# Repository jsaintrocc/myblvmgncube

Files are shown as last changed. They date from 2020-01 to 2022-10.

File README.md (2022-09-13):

# MY BLV MGN Cube

## Table of contents
  1. [Introduction](#introduction)
  2. [Bill of materials](manual/bom.md)
  3. [Printed parts](https://docs.google.com/spreadsheets/d/e/2PACX-1vTVx7BvB3V7CozF2l4eWkNntWrHSjOawmrsi_bRSVxQLIGVlfZTYEGp8a6fHpENV6hV2cn9PrDLHHl0/pubhtml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)
  4. [Print Settings](https://docs.google.com/spreadsheets/d/e/2PACX-1vTgPZb2P_rigplUG4TBjnBd7A5v86qJmxN26Bf9Z0P1HwILFovxDry4oiuArPlMLLYwE4DXcqXhaWn0/pubhtml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)
  5. [Assembly Guide](manual/guide/README.md)
  6. [License](#license)
  7. [Credits and inspiration](#credits-and-inspiration)

## Introduction
This documents my journey building the MGN BLV 3D Printer designed and graciously contributed to the world by [Ben Levi](parts/source/README.md). My goal is to provide a guide that others can follow to build their own cubes. This guide provides instructions for my specific build as detailed below. If your configuration is different keep that in mind when following the directions.

### Build Picture
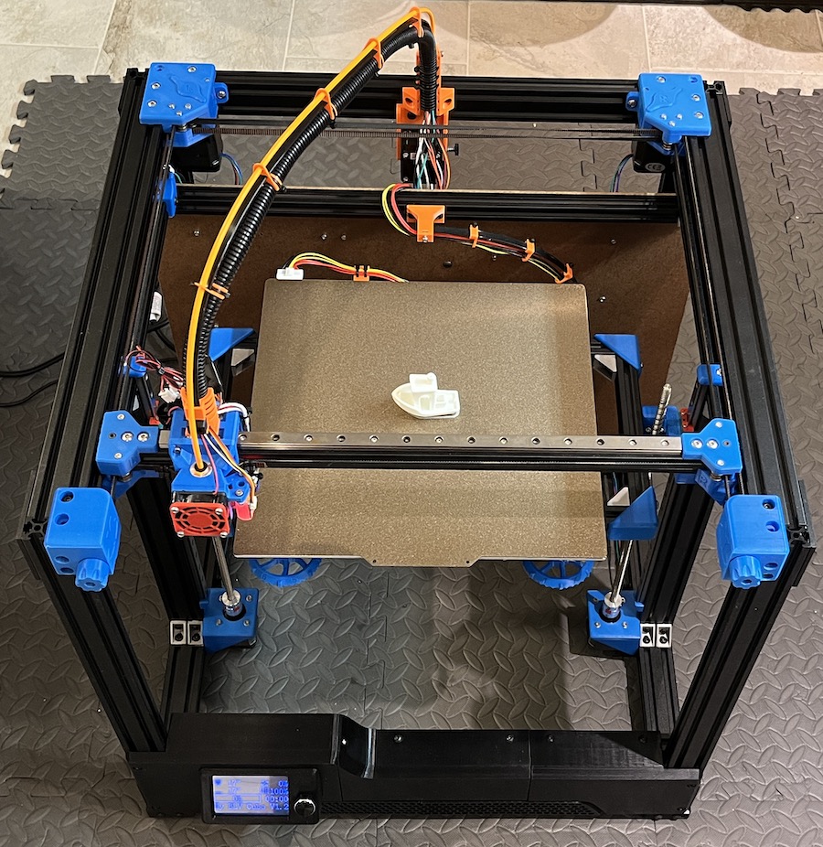
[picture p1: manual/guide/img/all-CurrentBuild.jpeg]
My Printer


### My Build Specifications
* Standard 365mm build height frame (The one listed on BLV's site)
* E3D V6 Cloned Hotend
* BLTouch ABL probe
* SKR v1.4 controller
* TMC2208 stepper drivers
* BIGTREETECH TFT35 <u>V3</u> LCD touch screen
* 3D printed parts

## License

Licensed under [CC BY-NC-SA 3.0](https://creativecommons.org/licenses/by-nc-sa/3.0/)

## Credits and inspiration
This work is based on the [BLV mgn Cube - 3d printer](https://www.blvprojects.com/blv-mgn-cube-3d-printer) graciously donated the the community by [Ben Levi](https://www.facebook.com/blevi?fref=gs&dti=371460246914851&hc_location=group_dialog) and is licensed under [CC BY-NC-SA 3.0](https://creativecommons.org/licenses/by-nc-sa/3.0/).  Any modified files will be clearly labelled.

Lots of tips and pointers from watching [Fugatech3D's live stream on his build](https://www.youtube.com/user/fuganater987)

Also the documentation and style modifications were greatly inspired by [Greg Saun's Work](https://github.com/gregsaun/bear_extruder_and_x_axis/blob/master/README.md)

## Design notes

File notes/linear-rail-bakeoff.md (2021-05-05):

# Liner Rail Bakeoff

## What's This Now?

I'm doing this to show some examples of the "economy" rails I've purchased and things to look out for. Linear rails for 3D printers are available at anywhere from $15/$200. Here's a detailed comparison of some of the lower end models I've purchased to hopefully provide some guidance and save you major headaches later on.

## TLDR

LDO would be my 1st pick followed by Robodigg and last would be CNA. For CNA I'd expect 2 out of 5 rails to be unusable and from the poor machining you'd probably introduce artifacts that would be very hard to fix. While Robotdigg is somewhat comparable keep in mind that coming from Aliexpress means to take a definite risk trying to return items and shipping times will be in weeks if not months.

### The Rails

| Part Number | Manufacturer | Cost + Shipping | Example Links |
|---|---|---|---|
| MGN12H 400mm Linear Rail | [CNA/RDBB](img/CNAManufacturer.JPG) (Cheap Cheap Cheap) | $20.92 | [Aliexpress](https://www.aliexpress.com/item/32829826159.html?spm=a2g0s.9042311.0.0.27424c4dwPelhS) |
| SS-MGN12-1H-400mm | RobotDigg (Middle Quality) | $34.20 | [Aliexpress](https://s.click.aliexpress.com/e/_AA8VKF) |
| LDO-MGN12H | LDO (Best Quality) | $34.80 (Free ship over $60) | [PrintedSolid](https://www.printedsolid.com/products/ldo-linear-rail-mgn12h-with-one-carriage-in-300-400-500-700mm-lengths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) [Filastruder](https://www.filastruder.com/products/ldo-linear-rails) [VRParts](https://vrparts.de/.../ldo-linearschienen-mgn12h-1r-l-400mm) |

### Tools I used

| Description | Details | Example Links |
|---|---|---|
| iPhone | What I took the pictures with | [Apple](https://www.apple.com/iphone/) |
| Clip-On Macro Lens | 20x Macro is what I used in this kit | [Amazon](https://amzn.to/3eeCqLU) |
| Smart Phone Tripod | To keep it steady | [Amazon](https://amzn.to/3dtMaTI) |

## Surface Finish Comparison On the Carriage

### End Finish

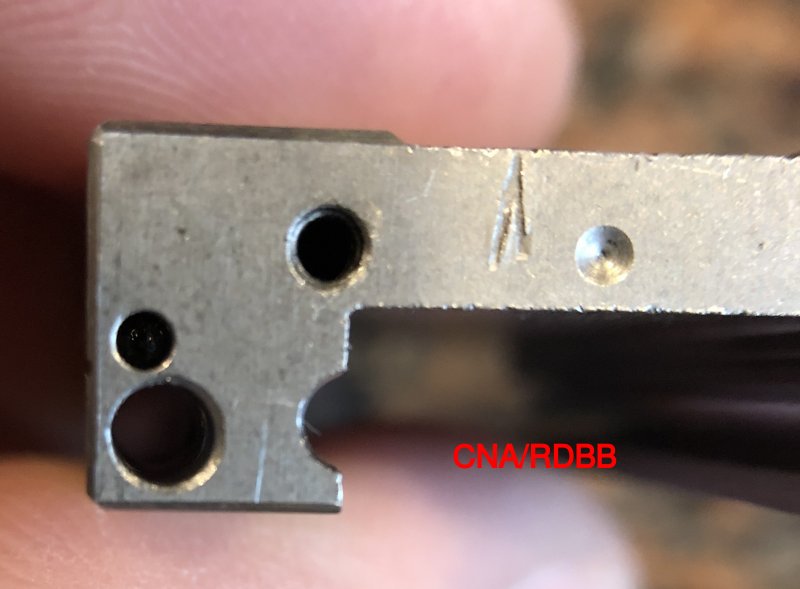
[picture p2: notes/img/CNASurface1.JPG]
CNARDBB Surface 1
 
**Surface is covered in marks. Even though it's cosmetic this one is particularly deep**

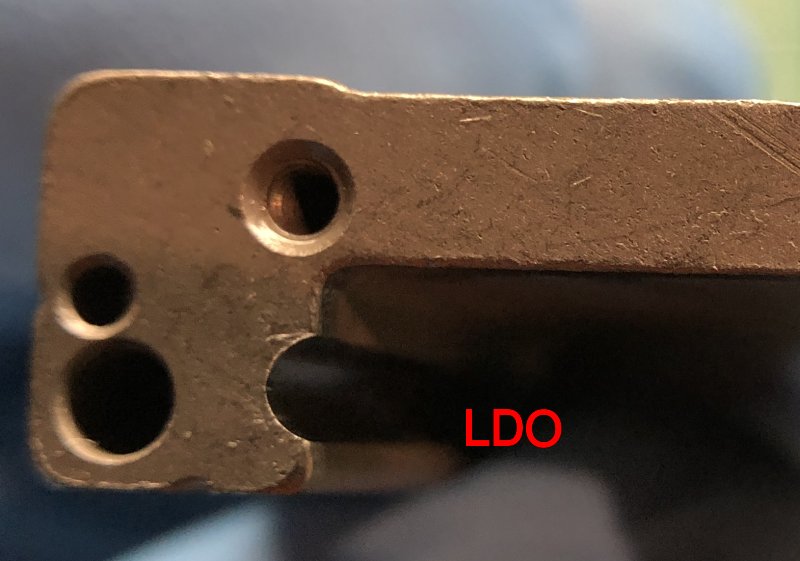
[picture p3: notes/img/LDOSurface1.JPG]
LDO Surface 1
 
**Similar tooling marks but nothing too deep**

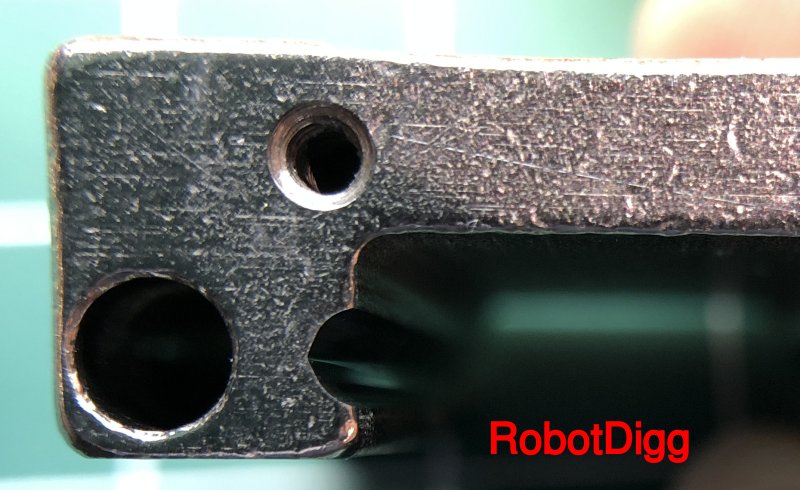
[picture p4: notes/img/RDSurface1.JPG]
RoboDigg Surface 1
 
**Many superficial scratches. There's a thick Chrome/Electroplated surface treatment here**

### Underside Finish

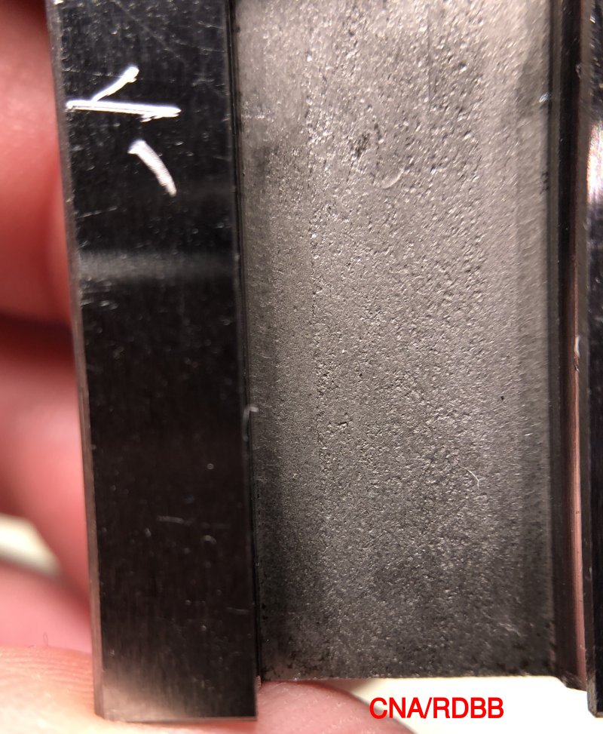
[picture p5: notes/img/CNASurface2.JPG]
CNARDBB Surface 2

**The grain in this picture really shows the poor quality of the alloy they're using. The mark in the upper left is actually engraved**

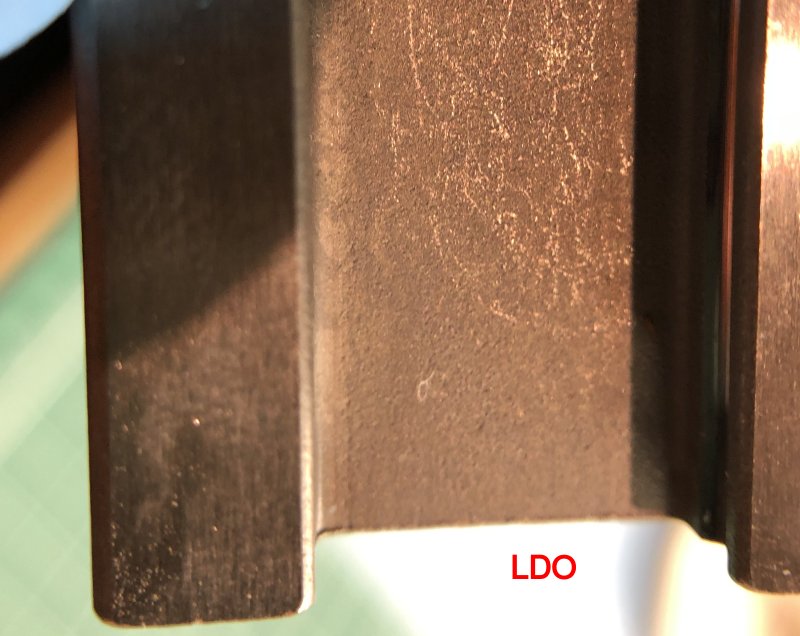
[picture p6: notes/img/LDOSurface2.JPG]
LDO Surface 2

**Little hard to see but the grain is much smaller and more consistent**

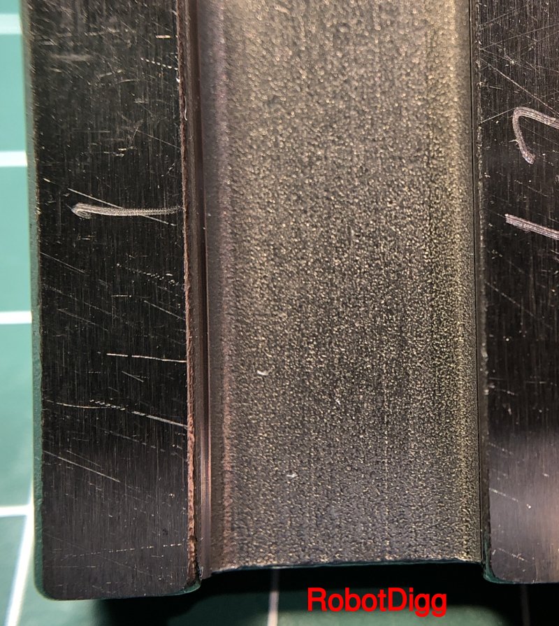
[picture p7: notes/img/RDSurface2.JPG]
RoboDigg Surface 2

**More of those etching marks but not too bad. However my 2nd carriage had some [missing Chrome on the underside](img/RDChromePlating.JPG)**

### Race/Return End Finish

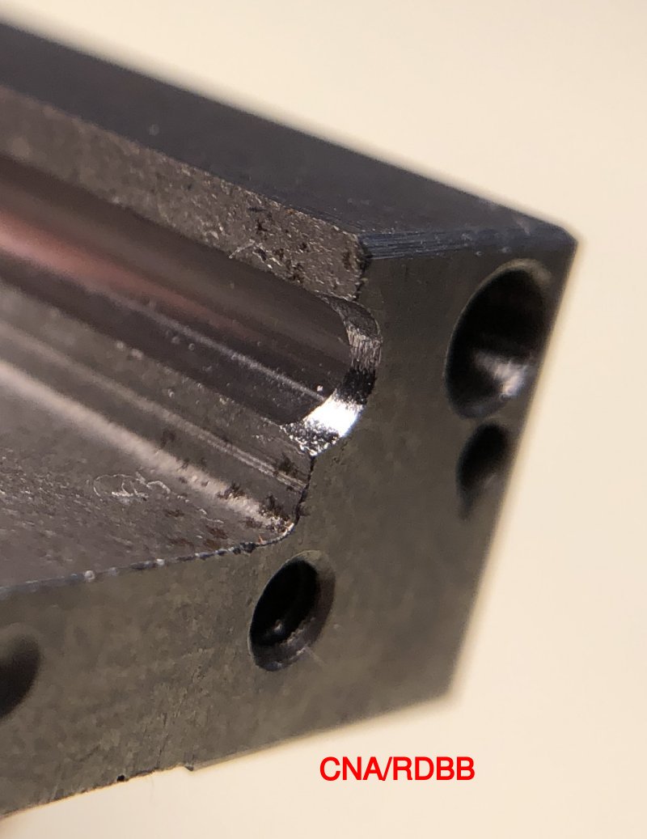
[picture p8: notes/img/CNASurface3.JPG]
CNARDBB Surface 3

**The alloy they're using is really terrible. Notice that the race has a hand filed bevel on it**

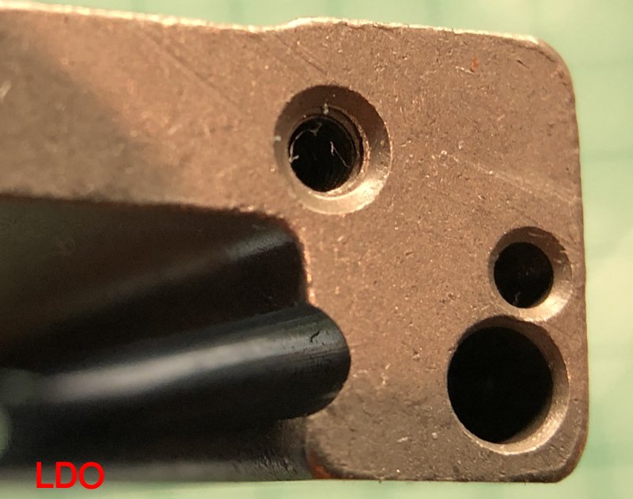
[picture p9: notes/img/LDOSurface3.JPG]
LDO Surface 3

**Here you can see that the machining is just better. The tolerances are much tighter**

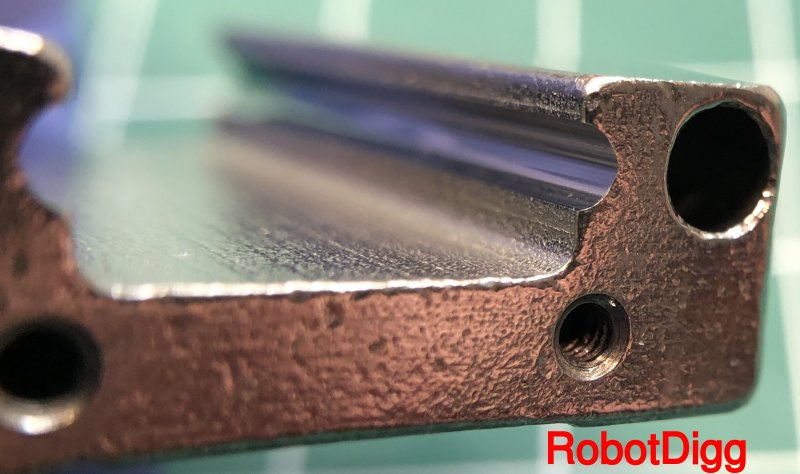
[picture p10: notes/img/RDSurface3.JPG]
LDO Surface 3

**Edges aren't very crisp. I'm guessing that's from the Chroming. This is less of an issue for RobotDigg because of something smart they did with PTFE liners. More on that later**

### Race Finish

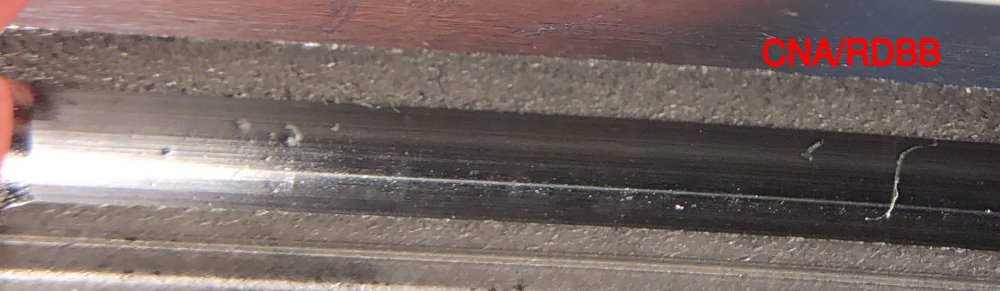
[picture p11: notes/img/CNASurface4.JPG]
CNARDBB Surface 4

**This is the important bit. Look at those pits and imperfections**

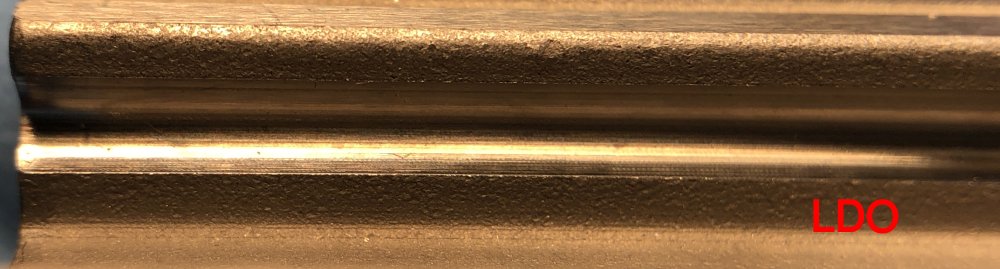
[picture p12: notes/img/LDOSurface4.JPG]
LDO Surface 4

**Machining on the race here is much better than CNA**

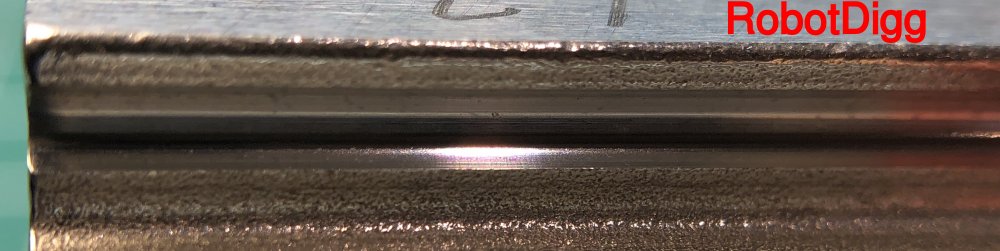
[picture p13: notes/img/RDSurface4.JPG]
RobotDigg Surface 4

**Machining on the race is comparable to LDO and much better than CNA. This is where the machining really counts!!**

### Ball Return Channels

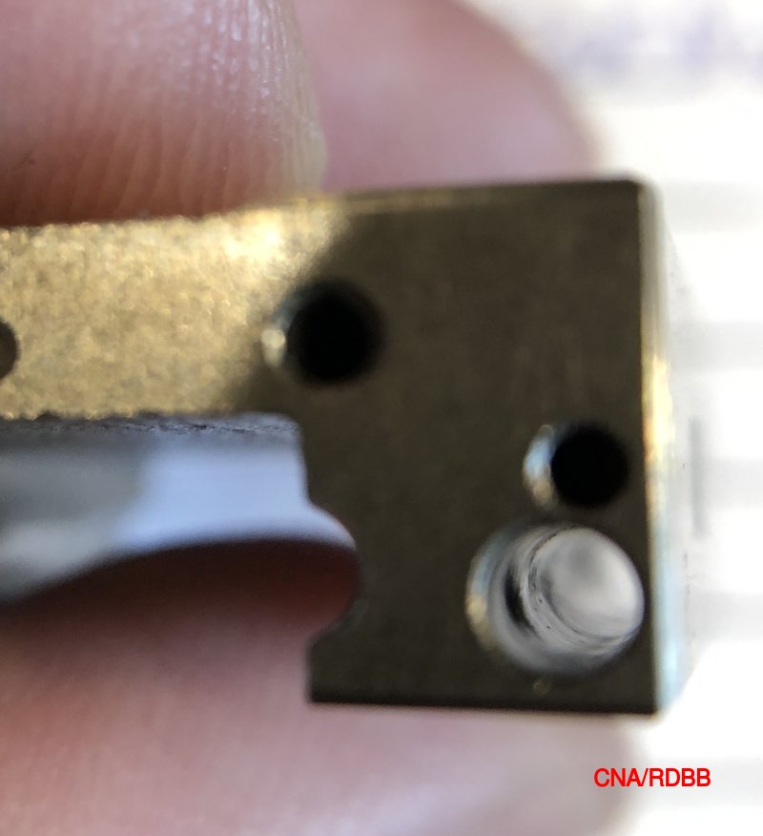
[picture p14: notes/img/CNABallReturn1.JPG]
CNARDBB Ball Return 1

**Look at those bumps. Bearings are not going to like that**

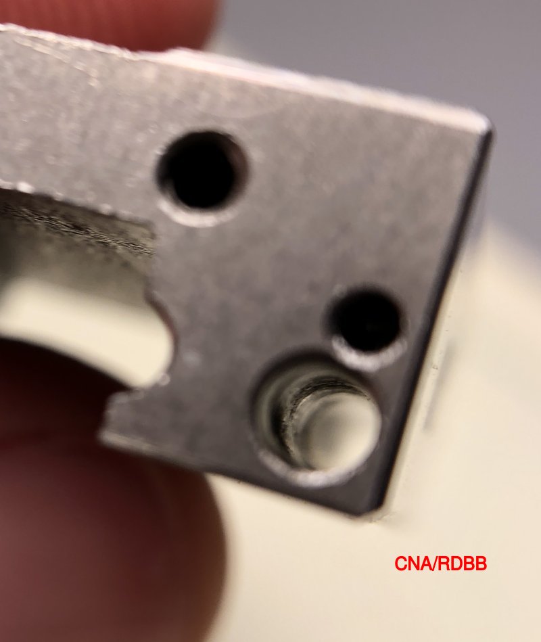
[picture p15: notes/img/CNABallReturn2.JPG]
CNARDBB Ball Return 2

**More bumps. Rough!!**

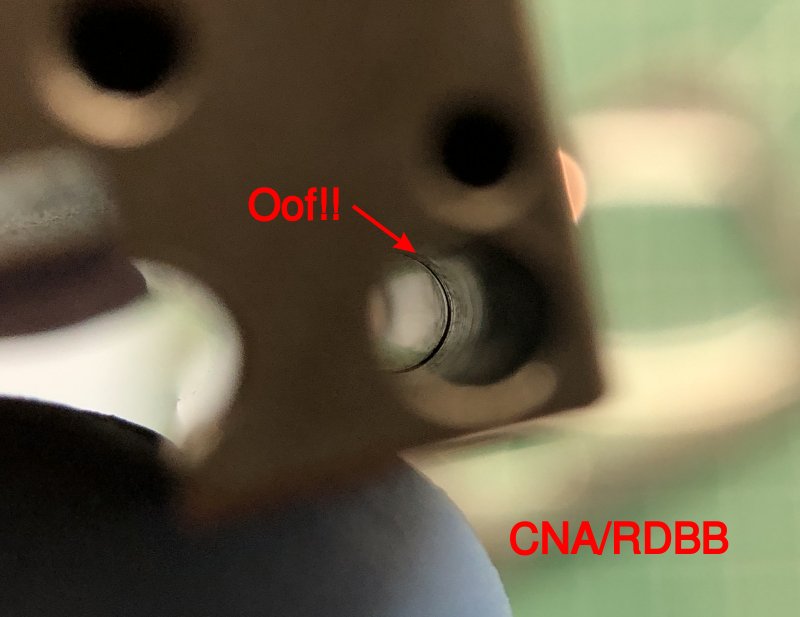
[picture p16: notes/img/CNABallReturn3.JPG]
CNARDBB Ball Return 3

**From a 2nd rail I got. That's a noticeable lip inside the ball return. This rail feels like gravel by the way**

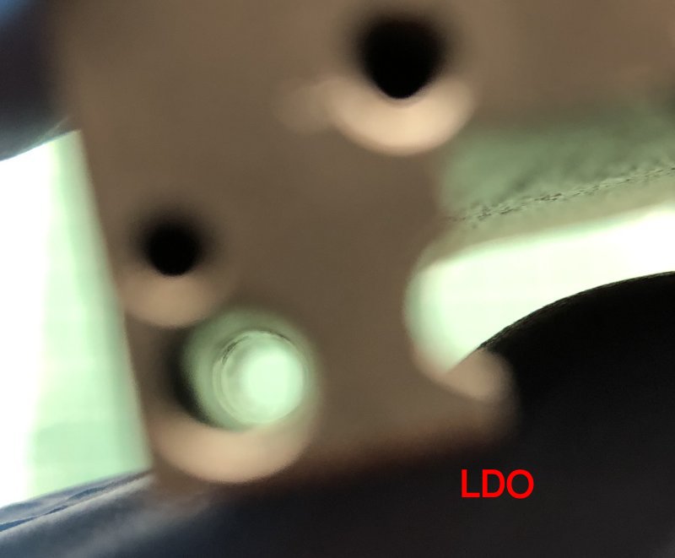
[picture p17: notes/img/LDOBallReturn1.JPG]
LDO Ball Return 1

**Not perfect but way better than CNA**

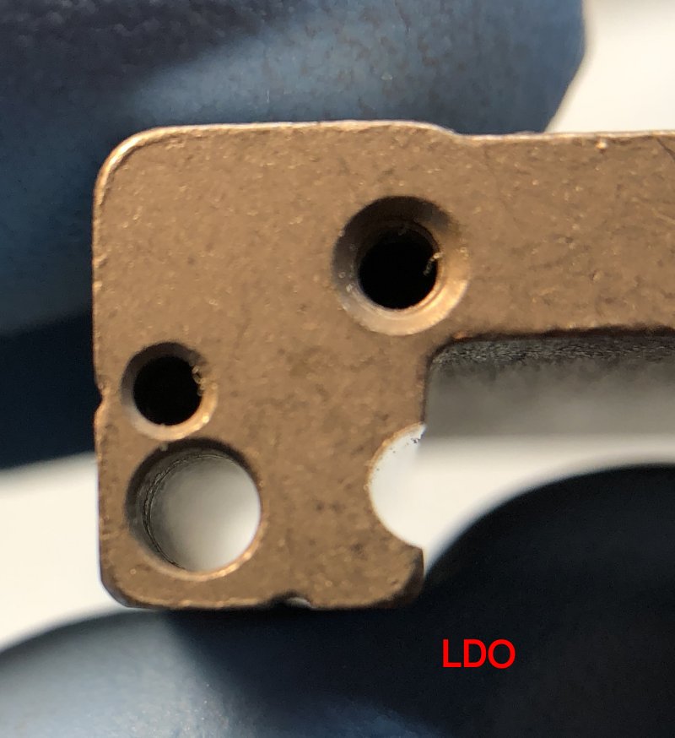
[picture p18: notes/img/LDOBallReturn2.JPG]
LDO Ball Return 2

**Not perfect but way better than CNA**

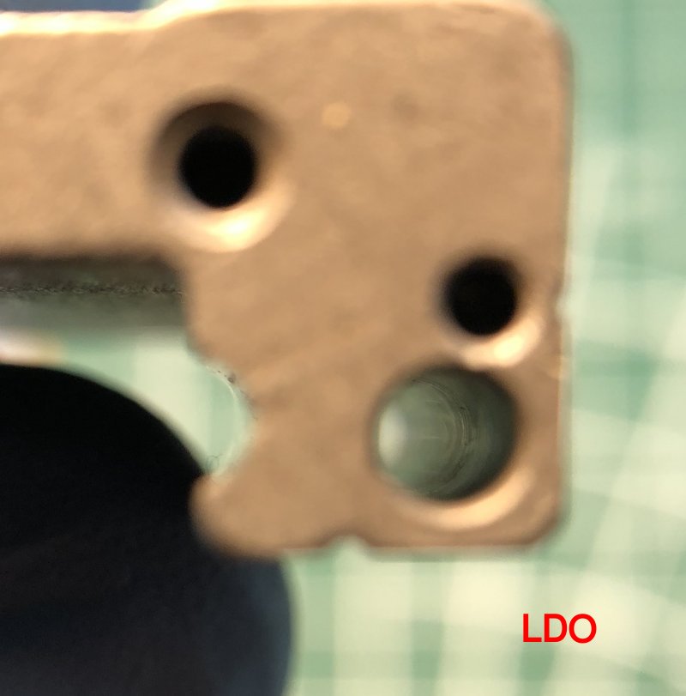
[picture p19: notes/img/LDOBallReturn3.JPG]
LDO Ball Return 3

**This one looks pretty good**

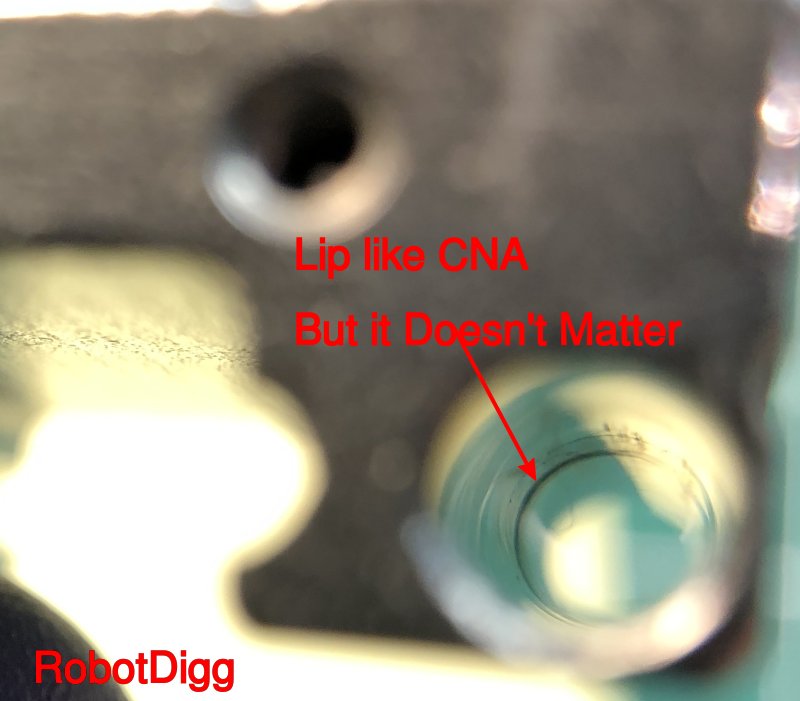
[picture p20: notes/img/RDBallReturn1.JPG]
RD Ball Return 1

**This shot doesn't really matter because of the smart engineering in the next step**

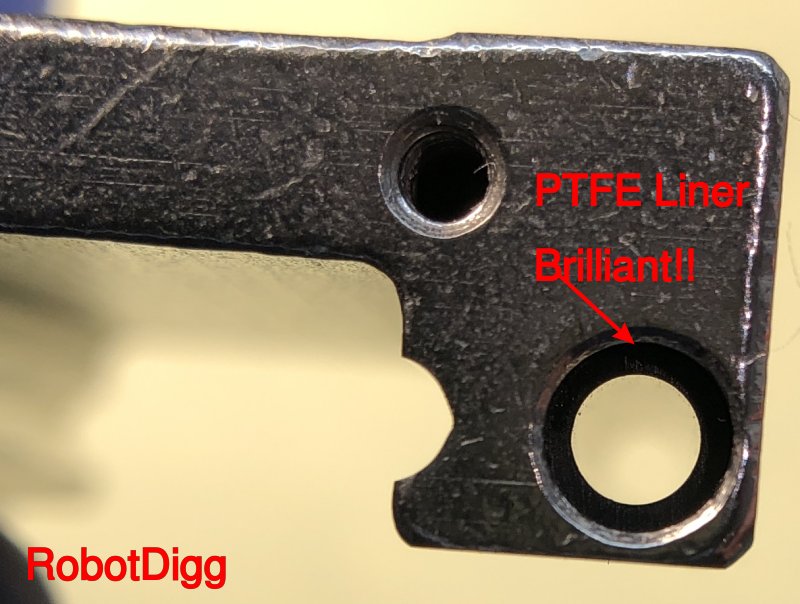
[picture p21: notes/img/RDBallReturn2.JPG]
RD Ball Return 2

**This liner means the machining isn't an issue and for our light application this will work great**

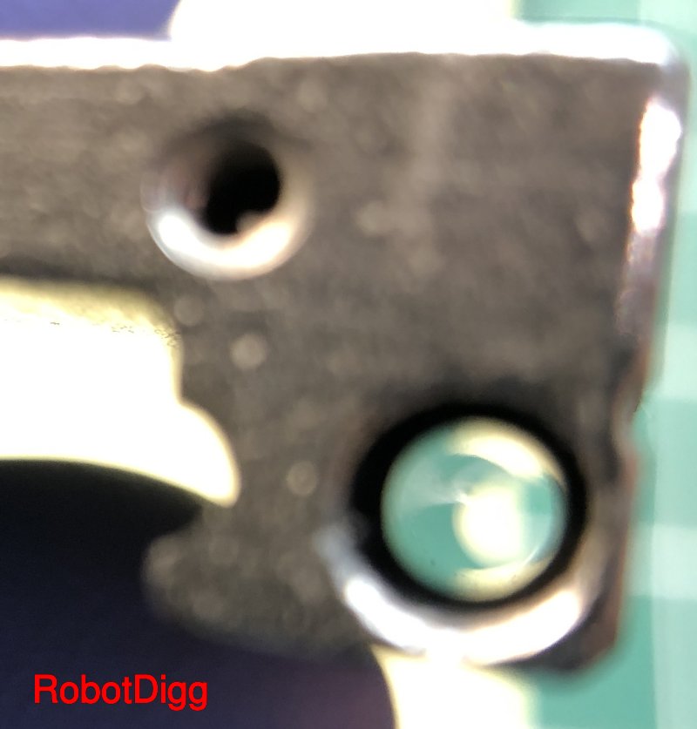
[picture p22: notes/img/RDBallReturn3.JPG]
RD Ball Return 3

**Hard to get a good shot as the liner is nearly mirror smooth**

### Ball Bearings

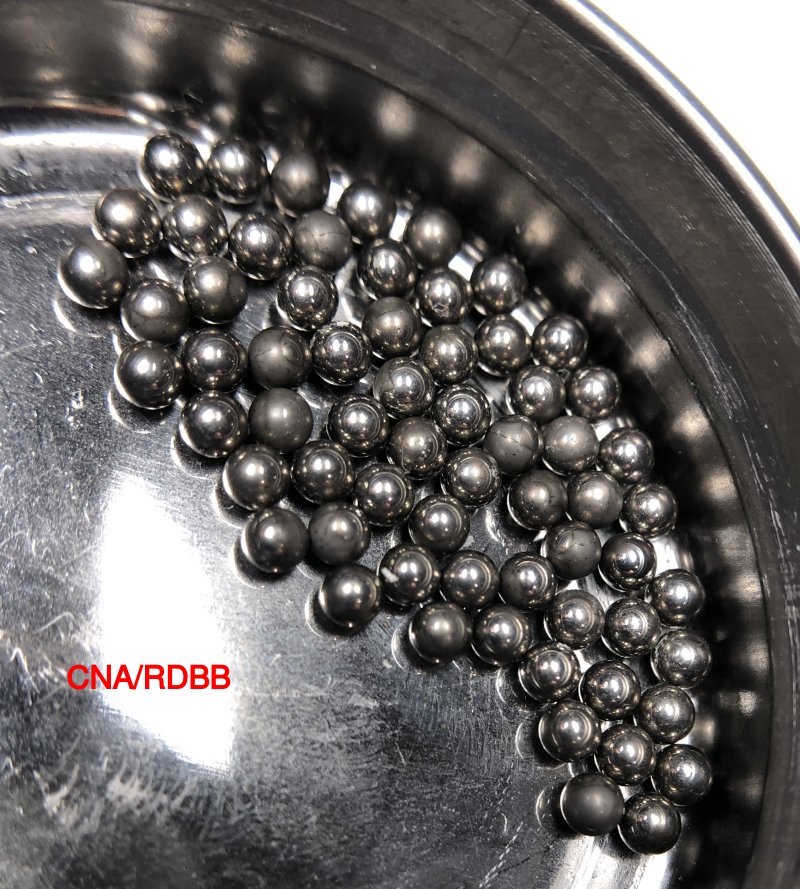
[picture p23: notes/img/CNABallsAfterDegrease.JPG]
CNARDBB Chrome Balls After Degrease

**Accidentally Left them in Simple Green overnight and this happened. Guessing this shows how thinly chromed they are**

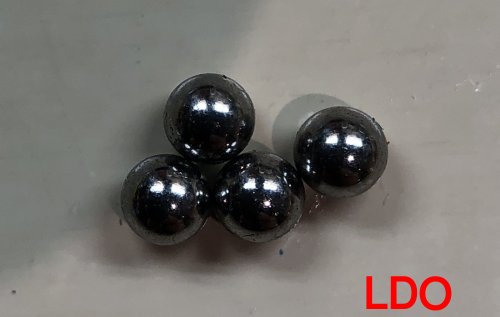
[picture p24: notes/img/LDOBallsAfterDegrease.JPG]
LDO Chrome Balls After Degrease

**Left them in Simple Green overnight to repeat the test. They're a little dirty but the chrome is in tact and under a magnifying glass they were good**

Robotdigg Chrome Balls After Degrease
**Didn't have any spare ball bearings for RobotDigg to do this test with**

## Bearing Size

| Manufacturer | Size in mm | Note |
|---|---|---|
| CNA/RDBB | 2.36 | Undersized |
| LDO | 2.37 | Closer to true 3/32 size and similar to the Amazon G25 grade bearings I bought |
| RobotDigg | 2.36 | Undersized |

## Verdict

The LDO linear rails had the best machining of the bunch and were comparable in price to the RobotDigg and worth the additional $15 over the CNAs. If you are in the USA you can get these from 2 reputable stores so shipping and returns will be much easier if you do have a problem. They'll definitely be my choice going forward.

While the RobotDigg had some good engineering with the PTFE linings and a couple other tricks on the end caps, the actual machining was not as good as the LDOs and they cost about the same. Also unlike the LDO and CNA rails there was no oil feeding port. That's not a huge issue as you can just put oil on the bearing directly in most cases. If you don't have access to the LDOs I'd choose the RobotDigg.

The CNA were by far the worst of the bunch. Machining was terrible and I think there is a lot of risk in using these on your 3d printer. They're super cheap but if you have to buy 1-3 rails and deal with returns to China it really isn't worth it. I'd worry about how long these will last given the quality of the bearings and what artifacts you might see.

## Additional Sources
https://www.youtube.com/watch?v=DMAx_JSMqGc
https://railcore.org/hardware/linear_rails.html

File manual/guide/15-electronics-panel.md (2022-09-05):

# My BLV MGN Cube - Step 15 Build Electronics Panel

## [Step 15 BoM Spreadsheet Link](https://docs.google.com/spreadsheets/d/e/2PACX-1vTVx7BvB3V7CozF2l4eWkNntWrHSjOawmrsi_bRSVxQLIGVlfZTYEGp8a6fHpENV6hV2cn9PrDLHHl0/pubhtml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)

### Prep
1. Cut a 440mm x 574mm rectangle out of the Tempered Hardboard using the Jig Saw.

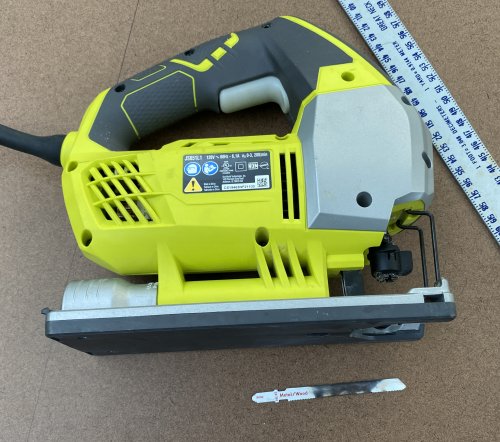
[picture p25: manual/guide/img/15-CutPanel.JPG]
    \
    *fig 15.1*

2. Attach Blue Tape and measure for holes on the both long edges at 95mm, 191mm, 287mm, 382mm, and 478mm.

    \
    *fig 15.2*

    \
    *fig 15.3*

### Assembly
1. Place 1x 576mm extrusion on top of the lower side rails and use the 2 man jigs to space it 60mm from the back extrusion.

    \
    *fig 15.4*

2. Attach the 576mm extrusion to the lower side rails using 2 brackets on left and right sides. 4 brackets total to attach the extrusion. They won't fit perfectly flush because of the alignment ridges but that's OK.

    \
    *fig 15.5*

    \
    *fig 15.6*

    Note: Official instructions call for 8 brackets, 2 front and back of each side of the extrusion. This is excessive/tricky and also gets in the way of the electronics panel.

3. Temporarily attach brackets to each side of the 2nd 576mm extrusion. The bracket should be flush on one side. These will help in the alignment in the next step

    \
    *fig 15.7*

    \
    *fig 15.8*

4. Clamp the 2nd 576mm extrusion to the bottom of the side extrusions with the linear rails attached to them. The 567mm extrusion should be parallel to the back extrusion and ~60mm apart from it.

    \
    *fig 15.9*

    \
    *fig 15.10*

5. Using the alignment tools on each side, position the top extrusion 60mm from the back extrusion.

    \
    *fig 15.11*

6. Using the 2 brackets attach the top extrusion on the left and right sides. Once the extrusion is secured remove the brackets you attached to help align the extrusion and reattach next to the other 2. There should be 2 brackets per side, all facing the front (same way as the bottom extrusion Fig 15.6).

    \
    *fig 15.12*

7. With the frame resting on it's front, rest the 440mm x 574mm Tempered Hardboard panel on the 2x 576mm extrusions you just attached. Clamp as shown in the picture.

    \
    *fig 15.13*

8. Using the 3D printed extruder mount as a guide, trace hole locations on the Blue Tape. Do this for the top and bottom of the panel. Just make sure the panel isn't warped when you do the bottom.

    \
    *fig 15.14*

9. Measure out mounting holes for the Din Rails and power supply location. **No middle rail**

   \
   *fig 15.15*

10. Using a Din Rail as a template, mark 3 mounting hole locations per rail.

    \
    *fig 15.16*

11. Create a mounting hole template for the power supply using blue tape. Update: Skip the middle DIN rail.

    \
    *fig 15.17*

13. Use the template on the Tempered Hardboard to mark the locations for the power supply mounting holes.

    \
    *fig 15.18*

14. Drill M4 sized holes (11/64" or ~4.5mm) for the power supply and drill M5 (7/32" or ~5.5mm) sized holes for everything else. You should have 4 M4 (Power Supply) and 19 M5 holes (Rails and Panel Mount).

    \
    *fig 15.19*

    Note: It can be helpful to drill a pilot hole with a much smaller bit (1/16" or 1.5mm). This will help you to drill the hole in the exact location you marked.

15. Clean up the holes using an X-Acto Knife.

    \
    *fig 15.20*

16. Mount the rails using M5 8mm Screws,washers (Only needed on the rail side) and Nuts. **No middle rail**

    \
    *fig 15.21*

    \
    *fig 15.22*

    Note: If the holes don't line up you can use the X-Acto Knife to widen or lengthen them.

17. Mount the Power Supply using the M4 6mm screws. Note: I only had M4 4mm flat head screws handy so that's what I used.

    \
    *fig 15.23*

    Note: If the holes don't line up you can use the X-Acto Knife to widen or lengthen them.

18. Here's what the front and back of the electronics panel should look like with everything mounted. Note that M5 8mm screws and T-Nuts have been put in the remaining holes. **Power supply should have terminals on top**

    \
    *fig 15.24*

    \
    *fig 15.25*

19. Now slide the panel onto the 576mm Extrusions and secure using the M5 8mm screws and T-Nuts.

    \
    *fig 15.26*

    \
    *fig 15.27*

20. Here's what the finished product should look like.

    \
    *fig 15.28*

    \
    *fig 15.29*

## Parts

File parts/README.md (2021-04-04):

# My BLV MGN Cube - Printed Parts

## Directory Contents
* Original Parts: [source](source)
* Remixed Parts: [remixed](remixed) *working on separating out original step files right now*
* Community Parts: [extra](extra) *improved parts from community members that are I used*
* Prusa Slicer 3MF files: [prusaslicer](prusaslicer) *The files I used to print my parts. Includes the supports I used etc..*

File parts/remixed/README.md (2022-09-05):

# Remixed Readme

## Description

This directory contains STL and Source files for parts I've created to fix issues I encountered when building my BLV MGN Cube. They are not part of the original source file distribution. Original source attribution [Ben Levi](../source/README.md)

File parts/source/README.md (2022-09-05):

Files in this directly are unmodified from the source files provided by Ben Levi as of 1/12/2020 on [www.blvprojects.com](https://www.blvprojects.com/blv-mgn-cube-3d-printer).  I've put them into subdirectories just to keep everything organized.

BLV mgn Cube - 3D Printer by BLV  (Ben Levi) is licensed under the
Creative Commons - Attribution - Non-Commercial - Share Alike license.

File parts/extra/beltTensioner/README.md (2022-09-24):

[Belt Tension Gauge with Weight](https://www.printables.com/model/278922-belt-tension-gauge-with-weight) by [James](https://www.printables.com/social/24267-james/about) on Printables

licensed under the [Creative Commons - Attribution - ShareAlike license](https://creativecommons.org/licenses/by-sa/4.0/).

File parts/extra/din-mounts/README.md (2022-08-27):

[Lerdge High Power Module (MOSFET) DIN Mount](https://www.printables.com/model/212718-lerdge-high-power-module-mosfet-din-mount) by [James](https://www.printables.com/social/24267-james/about) on Printables

[SKR 1.3/SKR 1.4/SKR 2.0 DIN Mount](https://www.printables.com/model/212719-skr-13skr-14skr-20-din-mount) by [James](https://www.printables.com/social/24267-james/about) on Printables

[Raspberry Pi 3/4 DIN Mount](https://www.printables.com/model/212720-raspberry-pi-34-din-mount) by [James](https://www.printables.com/social/24267-james/about) on Printables

[4010 Fan DIN Mount](https://www.printables.com/model/210873-4010-fan-din-mount) by [James](https://www.printables.com/social/24267-james/about) on Printables

licensed under the [Creative Commons - Attribution - Non-Commercial license](https://creativecommons.org/licenses/by-nc/4.0/).

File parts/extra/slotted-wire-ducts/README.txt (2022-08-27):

Slotted Wire Duct for 2020/2040 Extrusion (50mm -> 250mm) by jsaintrocc on Thingiverse: https://www.thingiverse.com/thing:5201239

licensed under theCreative Commons - Attribution - Non-Commercial - Share Alikelicense.

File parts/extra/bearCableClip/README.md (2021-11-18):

These files are provided here for convenience and are unmodified from the original source. They are the work of [Grégoire Saunier](https://github.com/gregsaun) and the [source code](https://github.com/gregsaun/prusa_i3_bear_upgrade/tree/master/printed_parts/common_to_all_versions/stl) is available as part of the [prusa i3 bear upgrade Project](https://github.com/gregsaun/prusa_i3_bear_upgrade).

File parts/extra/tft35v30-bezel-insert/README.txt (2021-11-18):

TFT35 V3.0 BLV MGN Cube Mount (Tweaked) by jsaintrocc on Thingiverse: https://www.thingiverse.com/thing:5024767

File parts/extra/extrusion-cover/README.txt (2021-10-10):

2020/2040 Extrusion Cover for V-Slot and T-Slot by jsaintrocc on Thingiverse: https://www.thingiverse.com/thing:4914054

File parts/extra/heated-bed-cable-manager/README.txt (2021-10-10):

 BLV MGN Cube Heated Bed Cable Manager by jsaintrocc on Thingiverse: https://www.thingiverse.com/thing:4965581

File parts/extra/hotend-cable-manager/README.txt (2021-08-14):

BLV MGN Cube Cable Manager by jsaintrocc on Thingiverse: https://www.thingiverse.com/thing:4932454

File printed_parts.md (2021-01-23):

## Work in Progress

Here is my working reference [Printed Parts Spreadsheet](../notes/Printed Parts Spreadsheet.xlsx)

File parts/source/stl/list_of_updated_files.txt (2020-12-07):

Left_motor_40mm_fan_mount.stl
Bed_Holder_-_Rear_right_For_CR-10_bed_M4_screw.stl
X_mount_-_Bottom_left.stl
Right_Z_motor_mount.stl
Right_corner_-_Top.stl
Front_Panel_-_Right_leds_diffuser.stl
Bed_Holder_-_Rear_right_For_Anet_E12_bed_M3_Screw.stl
Right_motor_40mm_fan_mount.stl
Right_corner_-_Block.stl
Front_Panel_-_Smartphone_drawer.stl
Front_Panel_-_left_grill.stl
Main_Cable_Tube_Holder.stl
Left_Tensioner_-_idler_holder.stl
Front_Panel_-_right_grill.stl
X_carriage_-_V6_Locker_BL-touch.stl
Bed_Holder_-_Rear_left_For_Anet_E12_bed_M3_Screw.stl
Left_Tensioner_-_mount.stl

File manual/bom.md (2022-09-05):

# MY BLV MGN Cube - Bill of Materials

## Summary
[Summary](https://docs.google.com/spreadsheets/d/e/2PACX-1vTVx7BvB3V7CozF2l4eWkNntWrHSjOawmrsi_bRSVxQLIGVlfZTYEGp8a6fHpENV6hV2cn9PrDLHHl0/pubhtml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)

## Grouped BoMs
* [Hardware BoM](https://docs.google.com/spreadsheets/d/e/2PACX-1vTVx7BvB3V7CozF2l4eWkNntWrHSjOawmrsi_bRSVxQLIGVlfZTYEGp8a6fHpENV6hV2cn9PrDLHHl0/pubhtml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)
* [Fasteners BoM](https://docs.google.com/spreadsheets/d/e/2PACX-1vTVx7BvB3V7CozF2l4eWkNntWrHSjOawmrsi_bRSVxQLIGVlfZTYEGp8a6fHpENV6hV2cn9PrDLHHl0/pubhtml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)
* [Tools BoM](https://docs.google.com/spreadsheets/d/e/2PACX-1vTVx7BvB3V7CozF2l4eWkNntWrHSjOawmrsi_bRSVxQLIGVlfZTYEGp8a6fHpENV6hV2cn9PrDLHHl0/pubhtml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)

## Pricing and Sourcing Details
* [Hardware Pricing](https://docs.google.com/spreadsheets/d/e/2PACX-1vTVx7BvB3V7CozF2l4eWkNntWrHSjOawmrsi_bRSVxQLIGVlfZTYEGp8a6fHpENV6hV2cn9PrDLHHl0/pubhtml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)
* [Fasteners Pricing](https://docs.google.com/spreadsheets/d/e/2PACX-1vTVx7BvB3V7CozF2l4eWkNntWrHSjOawmrsi_bRSVxQLIGVlfZTYEGp8a6fHpENV6hV2cn9PrDLHHl0/pubhtml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)
* [Tools Pricing](https://docs.google.com/spreadsheets/d/e/2PACX-1vTVx7BvB3V7CozF2l4eWkNntWrHSjOawmrsi_bRSVxQLIGVlfZTYEGp8a6fHpENV6hV2cn9PrDLHHl0/pubhtml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)

## Individual Steps
* [Step 1 BoM](guide/01-lubricate-mgn-rails.md#step-1-bom-spreadsheet-link)
* [Step 2 BoM](guide/02-build-y-rails.md#step-2-bom-spreadsheet-link)
* [Step 3 BoM](guide/03-frame-sides.md#step-3-bom-spreadsheet-link)
* [Step 4 BoM](guide/04-attach-frame-sides.md#step-4-bom-spreadsheet-link)
* [Step 5 BoM](guide/05-build-x-rail.md#step-5-bom-spreadsheet-link)  
* [Step 6 BoM](guide/06-build-tensioners.md#step-6-bom-spreadsheet-link)
* [Step 7 BoM](guide/07-hotend-carriage-a.md#step-7-bom-spreadsheet-link)
* [Step 8 BoM](guide/08-back-corners-a.md#step-8-bom-spreadsheet-link)
* [Step 9 BoM](guide/09-belts.md#step-9-bom-spreadsheet-link)
* [Step 10 BoM](guide/10-back-corners-b.md#step-10-bom-spreadsheet-link)
* [Step 11 BoM](guide/11-hotend-carriage-b.md#step-11-bom-spreadsheet-link)
* [Step 12 BoM](guide/12-z-axis-frame.md#step-12-bom-spreadsheet-link)
* [Step 13 BoM](guide/13-z-rails-motors.md#step-13-bom-spreadsheet-link)
* [Step 14 BoM](guide/14-heated-bed-frame.md#step-14-bom-spreadsheet-link)
* [Step 15 BoM](guide/15-electronics-panel.md#step-15-bom-spreadsheet-link)
* [Step 16 BoM](guide/16-hotend-wiring.md#step-16-bom-spreadsheet-link)
* [Step 17 BoM](guide/17-extruder-hotend-cable-manager.md#step-17-bom-spreadsheet-link)
* [Step 18 BoM](guide/18-heated-bed.md#step-18-bom-spreadsheet-link)
* [Step 19 BoM](guide/19-y-endstop.md#step-19-bom-spreadsheet-link)
* [Step 20 BoM](guide/20-front-panel.md#step-20-bom-spreadsheet-link)
* [Step 21 BoM](guide/21-wire-electric-panel.md#step-21-bom-spreadsheet-link)

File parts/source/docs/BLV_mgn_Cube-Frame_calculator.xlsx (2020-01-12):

BLV mgn Cube - Frame Calculator Beta
1 | Choose your Z height: | 365 | mm |  | < change here
2 | Choose your Heated bed size: |  | CR-10 310x310
Calculated Frame extrusion size
Qty | Item | Size | Units | Location
4 | 2040 aluminum extrusion | 560 | mm | corners height beams
9 | 2040 aluminum extrusion | 496 | mm | Wide Beams
2 | 2040 aluminum extrusion | 442 | mm | Z axis - mgn rails base
3 | 2020 aluminum extrusion | 576 | mm | Aux wide beams
1 | 2020 aluminum extrusion | 460 | mm | X axis beam
2 | 2020 aluminum extrusion | 405 | mm | Bed frame
2 | 2020 aluminum extrusion | 173 | mm | Bed frame
Mgn Rails
Qty | Item | Size | Units | Location
3 | Mgn12H Carriage + Rail | 400 | mm | X and Y axis
2 | Mgn12H Carriage + Rail | 400 | mm | Z axis
Mgn Rails
Qty | Item | Size | Units | Location
2 | Lead Screw 8mm 4 starts | 400 | mm | Z axis
If you find a mistake, please notify me: https://www.thingiverse.com/thing:3382718

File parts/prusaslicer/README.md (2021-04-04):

# My BLV MGN Cube - PrusaSlicer 3MFs

Theses are some of my prusa slicer project files.  There what I use and worked for me.  Useful step saver in terms of correct orientations etc...

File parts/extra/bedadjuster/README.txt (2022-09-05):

Creator: Tim Downs

Licensed to Tim Downs
 License: cc

Website: https://www.thingiverse.com/thing:3831053

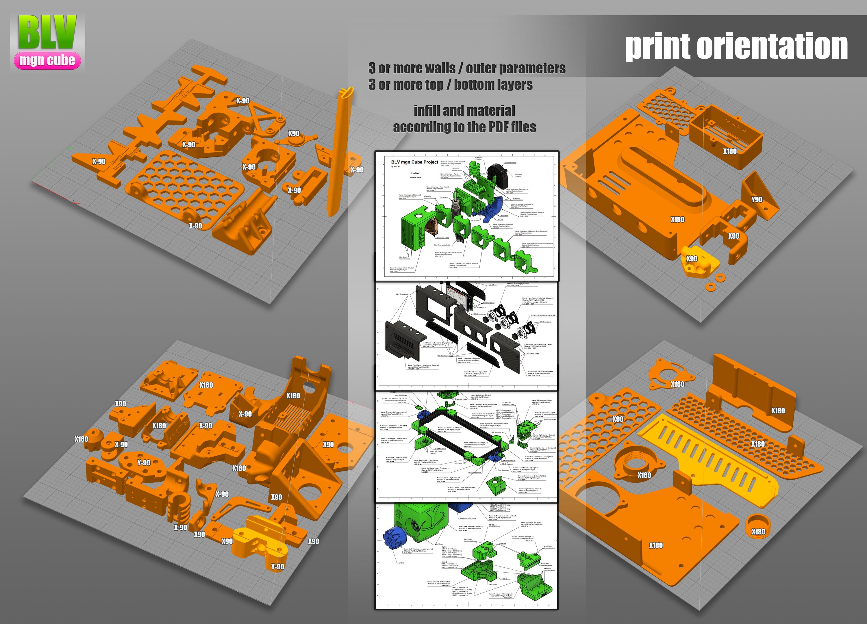
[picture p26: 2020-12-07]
parts/source/docs/PartsOrientation.jpg

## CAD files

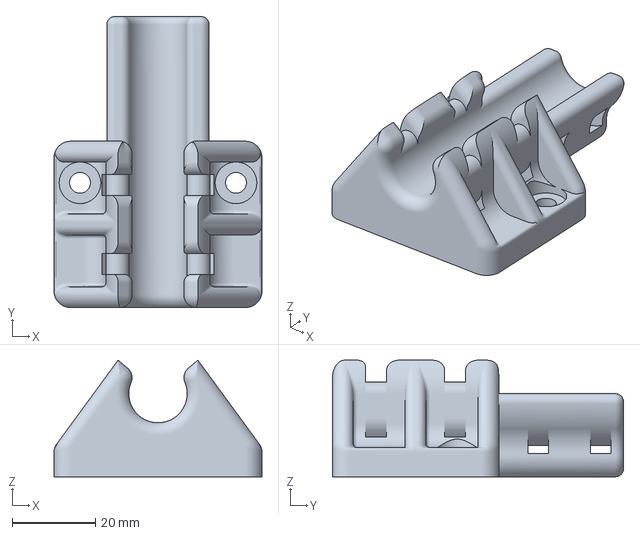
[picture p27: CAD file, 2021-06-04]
parts/prusaslicer/misc/abs/Main_Cable_Tube_Holder.3mf
50.0 x 70.0 x 28.0 mm

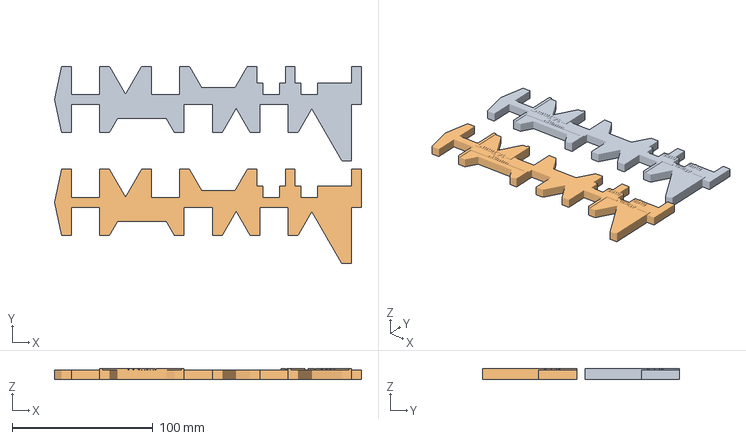
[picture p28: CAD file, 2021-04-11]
parts/prusaslicer/misc/pla/Jig_Main.3mf
217.8 x 140.0 x 8.00 mm
Jig_Main.stl x 2

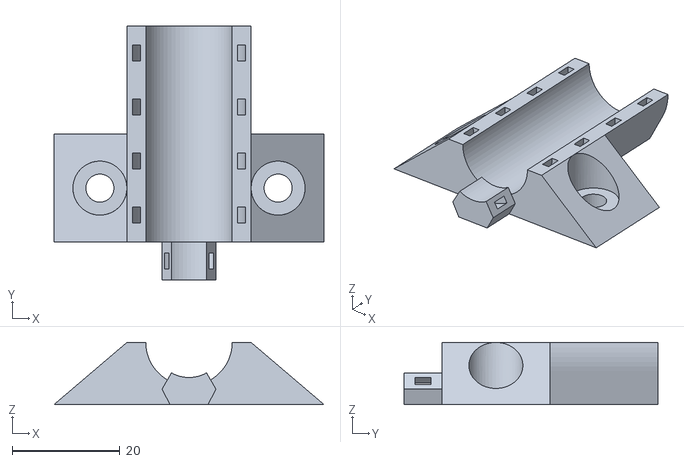
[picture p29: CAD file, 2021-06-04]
parts/remixed/stl/Main_Cable_Tube_Holder_JSR.stl
50.0 x 47.0 x 11.5

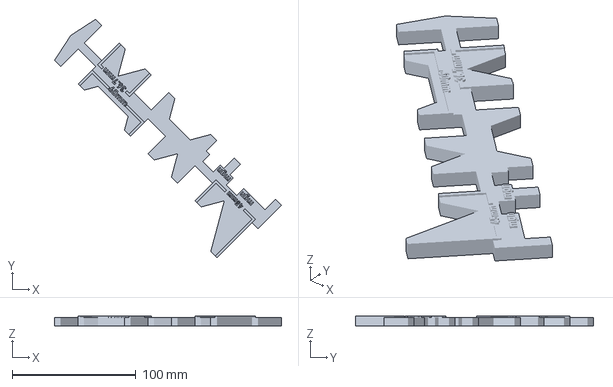
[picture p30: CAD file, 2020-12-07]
parts/prusaslicer/misc/abs/Jig_Main.3mf
183.7 x 192.9 x 8.00 mm

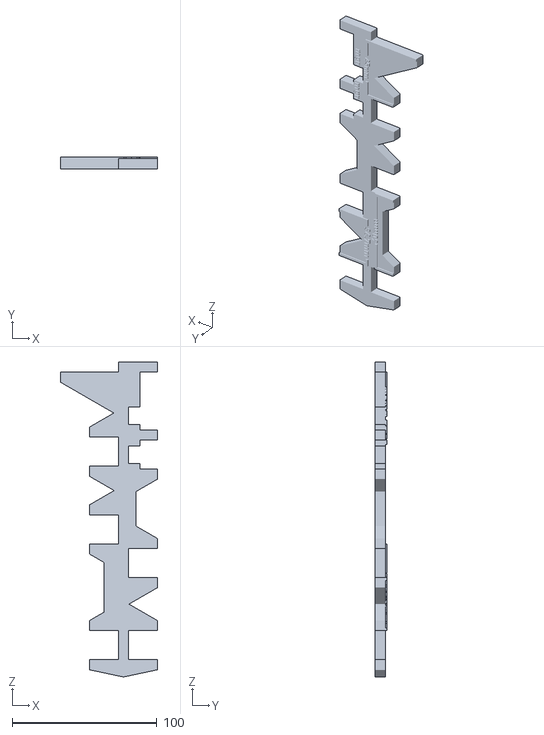
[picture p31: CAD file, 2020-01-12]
parts/source/stl/Jig_Main.stl
67.0 x 8.00 x 217.8

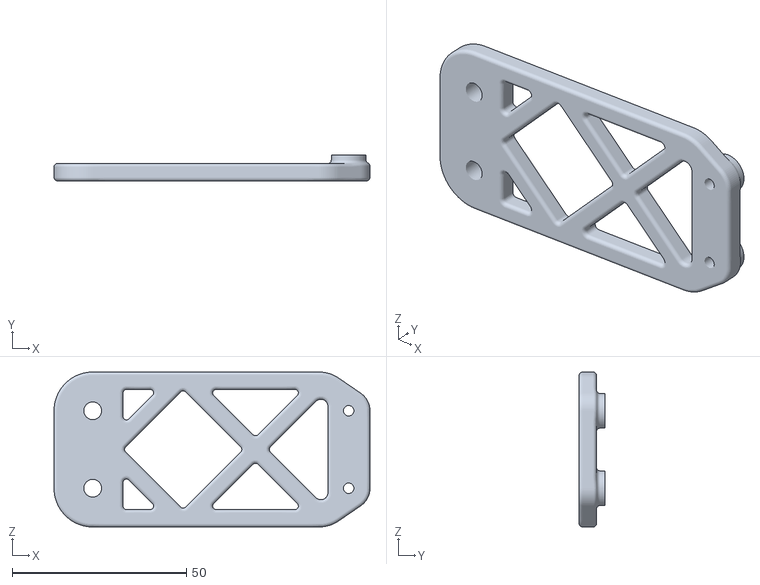
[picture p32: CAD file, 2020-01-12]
parts/source/stl/Nozzle_cleaner_-_main_holder.stl
90.8 x 7.40 x 44.5

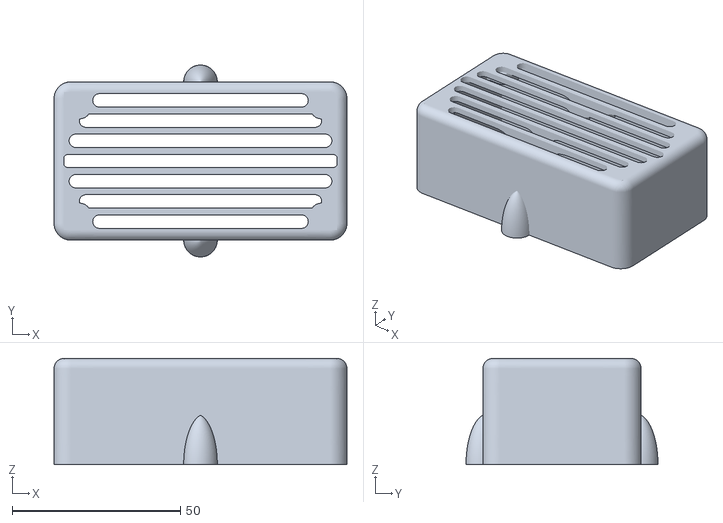
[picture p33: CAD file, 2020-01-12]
parts/source/stl/Air_scrubber_-_main_box.stl
87.0 x 57.0 x 31.5

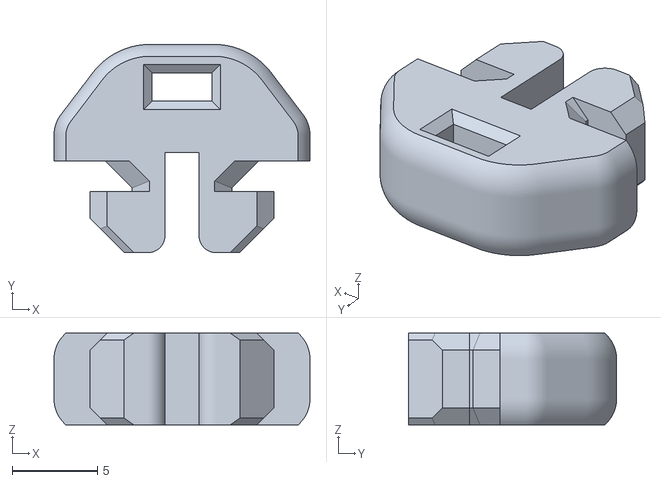
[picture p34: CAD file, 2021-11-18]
parts/extra/bearCableClip/cable_clip_horizontal.stl
15.1 x 12.2 x 5.40

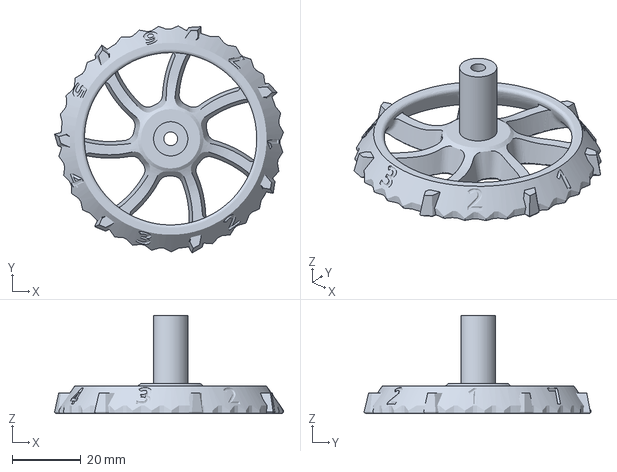
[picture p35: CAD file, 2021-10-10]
parts/extra/bedadjuster/BLV_Thumbwheel_bed_leveling_knob.3mf
66.8 x 66.3 x 28.6 mm

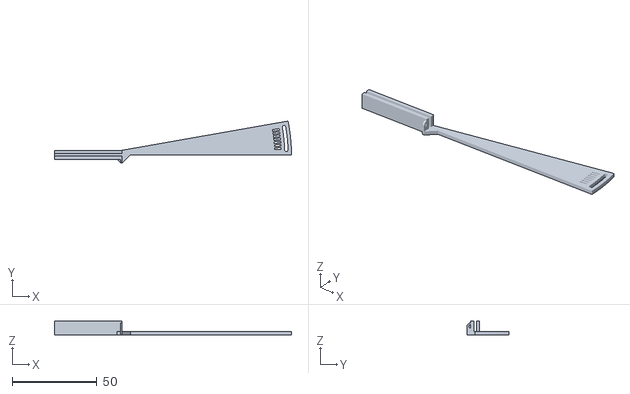
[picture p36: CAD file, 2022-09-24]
parts/extra/beltTensioner/GT2-6mm-Belt-Tension-Tool.stl
140.0 x 24.8 x 8.00

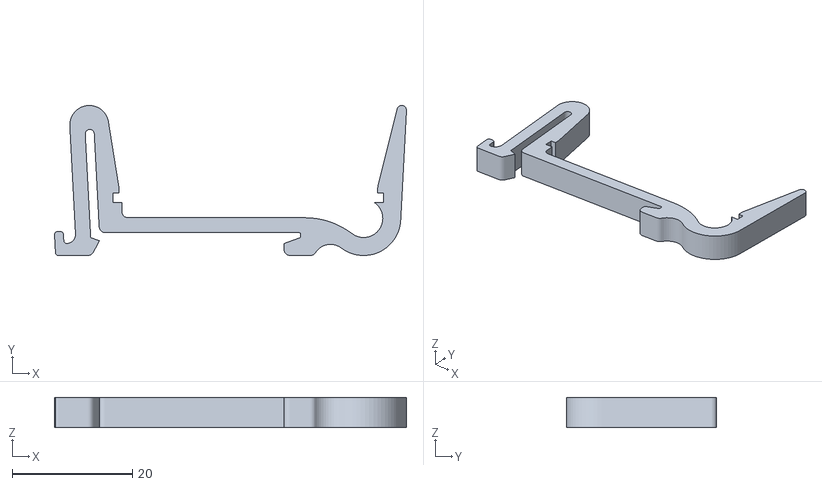
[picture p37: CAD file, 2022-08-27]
parts/extra/din-mounts/MOSFET_Mount.stl
58.6 x 25.0 x 5.00

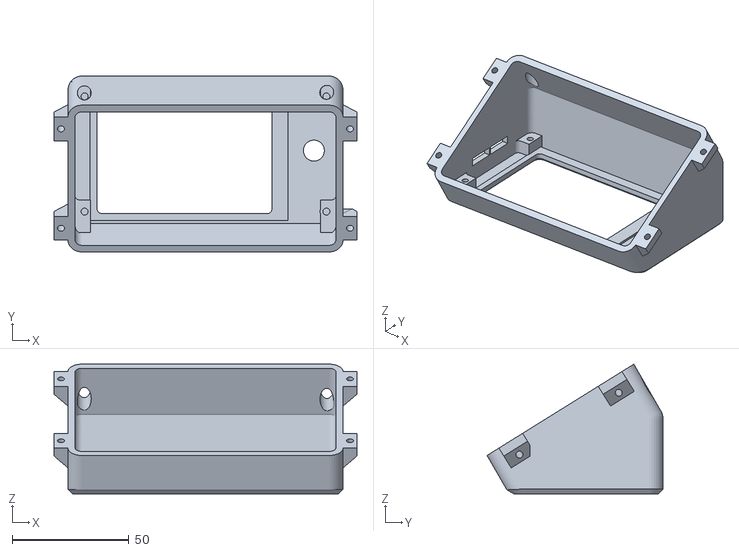
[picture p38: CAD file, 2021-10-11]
parts/extra/experimental/TFT32 V3.0 Mount v10.stl
130.0 x 75.5 x 55.7

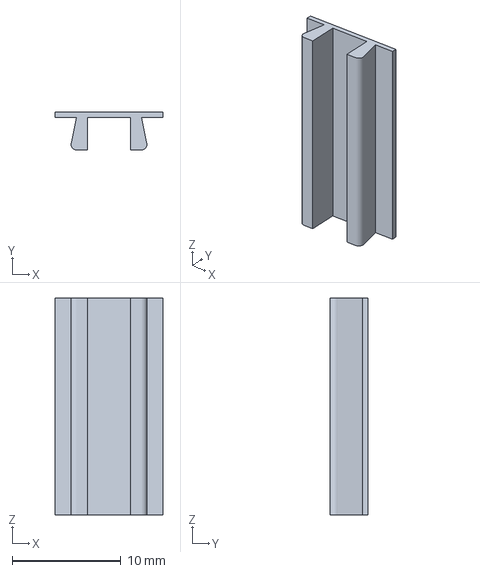
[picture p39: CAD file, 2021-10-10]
parts/extra/extrusion-cover/extrusion-cover.3mf
10.0 x 3.50 x 20.0 mm

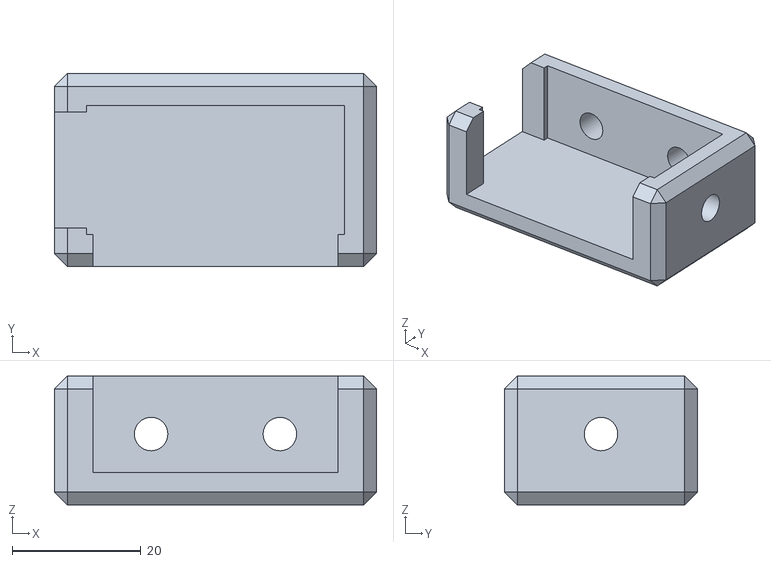
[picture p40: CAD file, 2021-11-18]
parts/extra/feet/FootLv3.stl
50.0 x 30.0 x 20.0

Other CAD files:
parts/source/stl/Main_Cable_Tube_Holder.stl
parts/extra/heated-bed-cable-manager/heatbed-wireguide-loop.stl
parts/extra/hotend-cable-manager/files/flex-tube-reinforcer.stl
parts/extra/improved-bezel/files/Front_Panel_-_Left_plate_for_TFT35_V2.STL
parts/extra/bearCableClip/cable_clip_vertical.stl
parts/extra/bedadjuster/BLV_Thumbwheel_bed_leveling_knob.stl
parts/extra/beltTensioner/X-Carriage-Clamp.stl
parts/extra/din-mounts/4010_MountThick.stl
parts/extra/din-mounts/MOSFET_Long2.stl
parts/extra/din-mounts/rPi_DIN_Mount_v4.stl
parts/extra/din-mounts/skr14_Mount2.stl
parts/extra/experimental/TFT32 V3.0 Mount v4.stl
parts/extra/experimental/TFT32 V3.0 Mount v5.stl
parts/extra/experimental/TFT32 V3.0 Mount v6.stl
parts/extra/experimental/TFT32 V3.0 Mount v7.stl
parts/extra/experimental/TFT32 V3.0 Mount v8.stl
parts/extra/experimental/Wire Clamp.stl
parts/extra/experimental/Wire Clamp2.stl
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

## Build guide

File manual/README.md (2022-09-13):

# My BLV MGN Manual

## Table of Content

1. [Bill Of Materials](bom.md)
2. [Print Settings](https://docs.google.com/spreadsheets/d/e/2PACX-1vTgPZb2P_rigplUG4TBjnBd7A5v86qJmxN26Bf9Z0P1HwILFovxDry4oiuArPlMLLYwE4DXcqXhaWn0/pubhtml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)
3. [Printed Parts STLs](https://docs.google.com/spreadsheets/d/e/2PACX-1vTVx7BvB3V7CozF2l4eWkNntWrHSjOawmrsi_bRSVxQLIGVlfZTYEGp8a6fHpENV6hV2cn9PrDLHHl0/pubhtml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)
4. [Assembly Guide](guide/README.md)
5. [Sources](../parts/README.md)

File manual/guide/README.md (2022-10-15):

# MY BLV MGN Cube - Assembly Guide

## Table of Content

1. [Lubricate MGN Linear Rails](01-lubricate-mgn-rails.md)
2. [Build Y Rails](02-build-y-rails.md)
3. [Build Frame Sides](03-frame-sides.md)
4. [Attach Frame Sides](04-attach-frame-sides.md)
5. [Build X Rail](05-build-x-rail.md)
6. [Build Tensioners](06-build-tensioners.md)
7. [Partially Build Hotend Carriage](07-hotend-carriage-a.md)
8. [Partially Build Back Corners](08-back-corners-a.md)
9. [Install Belts](09-belts.md)
10. [Finish Building Back Corners](10-back-corners-b.md)
11. [Finish Building Hotend Carriage](11-hotend-carriage-b.md)
12. [Build Z-Axis Frame](12-z-axis-frame.md)
13. [Build Z Rails and Motors](13-z-rails-motors.md)
14. [Build Heated Bed Frame and Finish Z-Axis](14-heated-bed-frame.md)
15. [Build Electronics Panel](15-electronics-panel.md)
16. [Wire Hotend](16-hotend-wiring.md)
17. [Build Bowden Extruder and Hotend Cable Manager](17-extruder-hotend-cable-manager.md)
18. [Install and Wire the Heated Bed](18-heated-bed.md)
19. [Mount Y Endstop](19-y-endstop.md)
20. [Build Front Panel](20-front-panel.md)
21. [Wire Electric Panel](21-wire-electric-panel.md)
22. [Tension Belts](22-tension-belts.md)
23. [Setup RaspberryPi and SKR Controller](23-setup-rPi-skr-board.md)

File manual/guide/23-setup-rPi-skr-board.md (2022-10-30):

# My BLV MGN Cube - Step 23 Setup OctoPrint and Klipper

## [Step 23 BoM Spreadsheet Link](https://docs.google.com/spreadsheets/d/e/2PACX-1vTVx7BvB3V7CozF2l4eWkNntWrHSjOawmrsi_bRSVxQLIGVlfZTYEGp8a6fHpENV6hV2cn9PrDLHHl0/pubhtml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)

### Procedure
1. Install OctoPi on your RaspberryPi (rPi) by following the [Official OctoPi Instructions](https://octoprint.org/download/#octopi) and the notes below.
   * Use the OctoPi 32GB microSD card
   * Use RaspberryPi installer and selected "OctoPi (stable)" from the "Other specific-purpose OS"
   * Select the gear icon and pre-configure the image
     * Set hostname: blvcube.local (Or whatever you want to name your printer)
     * Enable SSH
     * Set Username and Password: Keep 'pi' username but pick a unique password
     * Configure Wireless LAN: Your wifi settings
     * Do the locale info for your region

2. Insert the OctoPi MicroSD card and turn on your rPi. 
3. Find the IP of the RaspberryPi
   ```shell
   nslookup blvcube
   ```
   Note: If that doesn't work try `blvcube.lan` or `blvcube.local` otherwise you'll have to login to your wifi router and find out what IP it assigned to it.

4. Login to OctoPrint "Ex. [http://blvcube](http://blvcube)" and go through the setup. BLV Cube specific configs are below.
   * Default Printer Profile
      * General
        * Name: BLVCube
        * Model BLV Cube
      * Print bed & build volume
        * Form Factor: Rectangular
        * Origin: Lower Left
        * Width (X): 310.0
        * Depth (Y): 310.0
        * Height (Z): 345.0 
        * Custom bounding box: false
      * Axes
        * X: 6000 mm/min Invert control: false
        * Y: 6000 mm/min Invert control: false
        * Z: 200 mm/min Invert control: false
        * E: 300 mm/min Invert control: false
      * Hotend & extruder
        * Nozzle Diameter: 0.4 mm
        * Number of Extruders: 1
        * Default extrusion length: 5mm

5. Install klipper software on the rPi.
   1. Use SSH to connect to the rPi with the username "pi" and the password you chose.
   2. Download and install Klipper.
      ```shell
      git clone https://github.com/Klipper3d/klipper
      ./klipper/scripts/install-octopi.sh
      ```
      Reference: [Klipper instructions](https://www.klipper3d.org/Installation.html#prepping-an-os-image)
6. Configure OctoPrint to talk to Klipper daemon using the following serial port settings:
   * Serial Port: /tmp/printer
   * Baudrate: 250000
   * Auto-connect to printer on server start: Checked

7. Test the config by connecting to the printer from OctoPrint. You should see something like this in the Terminal tab:
   ```
   Connecting to port /tmp/printer, baudrate 250000
   Changing monitoring state from "Opening serial connection" to "Connecting"
   Connected to: Serial<id=0xa8e242b0, open=True>(port='/tmp/printer', baudrate=250000, bytesize=8, parity='N', stopbits=1, timeout=10.0, xonxoff=False, rtscts=False, dsrdtr=False), starting monitor
   Send: N0 M110 N0*125
   Recv: ok
   Send: N0 M110 N0*125
   Changing monitoring state from "Connecting" to "Operational"
   Recv: ok
   Send: N0 M110 N0*125
   Recv: ok
   Send: N1 M115*39
   Recv: ok FIRMWARE_VERSION:v0.10.0-594-g7290c145 FIRMWARE_NAME:Klipper
   Send: M21
   Recv: ok
   Send: M105
   Recv: ok T:0
   ```
   Note: This just tells us that OctoPrint is talking to the Klipper service on the rPi. We haven't setup the controller board yet so any errors like "!! mcu 'mcu': Unable to connect" are normal for now.

8. Build the firmware for the SKR 1.4 Turbo using [this guide](https://docs.vorondesign.com/build/software/skr13_klipper.html)
9. Copy the binary file in `~/klipper/out/klipper.bin` to the klipper microSD card and rename to `firmware.bin`.
   Easiest way to do this is to use `scp` to copy the bin to your machine and from there copy it on to the microSD card.
10. Install the klipper firmware on the SKR 1.4 Turbo controller board.
    1. Insert the klipper microSD card into the controller board and power on.
    2. The controller board will automatically flash the onboard memory using the firmware.bin on the SD card.
    3. If you remove the microSD card and see a file named "FIRMWARE.CUR" the flashing was successful.

11. Install the klipper config
    1. scp the config to the rPI (the tgz is in the configs directory).
        ```shell
        scp configs/klipper-cfg-basic.tgz pi@blvcube:
        ```
    2. Login to the rPi and extract the tarball.
       ```shell
       tar xzvf klipper-cfg-basic.tgz
       ```
    3. Configure the rPi klipper service to talk to your controller via the serial port.
       
       1. Power on the controller board.
          ```shell
          ls /dev/serial/by-id/* | grep -i klipper
          ```
          You should see something like this:
          ```shell
          /dev/serial/by-id/usb-Klipper_lpc1769_02D0000EC09869AFADCA405EC02000F5-if00
          ```
       2. Edit the printer.cfg file and update the `serial` parameter under the `[mcu]` heading.
       
          Example:
          ```
          [mcu]
          serial: /dev/serial/by-id/usb-Klipper_lpc1769_02D0000EC09869AFADCA405EC02000F5-if00

          ```
          
       3. Restart klipper to reread the config by typing `RESTART` in the OctoPrint Terminal.
       4. You should now start seeing real temperature messages in the Terminal which means the Klipper is now communicating with the controller.
          ```shell
          Send: M105
          Recv: ok B:19.9 /0.0 T0:21.2 /0.0
          Send: M105
          Recv: ok B:19.9 /0.0 T0:21.1 /0.0
          ```
          
12. Time to test the printer!! Run `G28` in a terminal and see what happens. I HIGHLY RECOMMEND you have your finger on the power button and watch this VERY CAREFULLY.

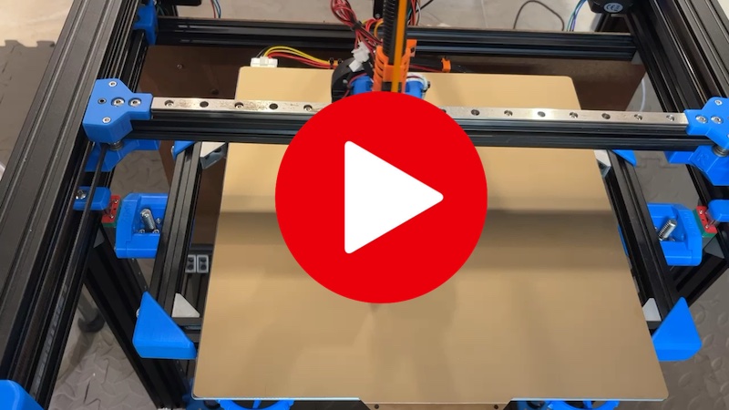
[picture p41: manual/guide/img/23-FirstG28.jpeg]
(https://youtu.be/UrhKAm_vww0)
    \
    *fig 23.1*

### Appendix: Restart Klipper on Controller Connection
The Klipper service only connects to the controller when the service starts. This means if you leave the rPi on and separately turn the controller on/off you will need to restart klipper every time. This is annoying if you use OctoPrint to control your Cube's power. This workaround will automatically restart Klipper any time the rPi detects that the controller has connected via it's serial port.

1. Add rule to rules.d to auto restart klipper when the controller board reboots.
   1. Find the Vendor ID and Product ID
      ```shell
      sudo lsusb -v 2>&1 | grep -E 'iManufacturer|idVendor|idProduct' | grep -B2 'Klipper' 
      ```
      Ex.
      ```shell
      idVendor           0x1d50 OpenMoko, Inc.
      idProduct          0x614e
      iManufacturer           1 Klipper
      ```
   2. Edit /etc/udev/rules.d/98-klipper.rules.
      ```shell
      ## rule to restart klipper when the printer is connected via usb
      SUBSYSTEM=="usb", ATTRS{idVendor}=="1d50", ATTRS{idProduct}=="614e", ACTION=="add", RUN+="/bin/su pi -c '/bin/echo RESTART > /tmp/printer'"
      ```
      Replace "id50" and "614e" with your information if it's different
   3. Reload the rules when you are done.
      ```shell
      udevadm control --reload-rules
      systemctl restart systemd-udevd.service
      ```

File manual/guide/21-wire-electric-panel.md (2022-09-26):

# My BLV MGN Cube - Step 21 Wire Electronics Panel

## [Step 21 BoM Spreadsheet Link](https://docs.google.com/spreadsheets/d/e/2PACX-1vTVx7BvB3V7CozF2l4eWkNntWrHSjOawmrsi_bRSVxQLIGVlfZTYEGp8a6fHpENV6hV2cn9PrDLHHl0/pubhtml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)

### Prep
1. Assemble the slotted wire ducts.
   1. The Sides should click onto pegs on the bottom. 
   2. Heat the nail head, using the candle, and heat weld all the pegs.
   3. I used a twisting motion so the nail wouldn't stick.
   
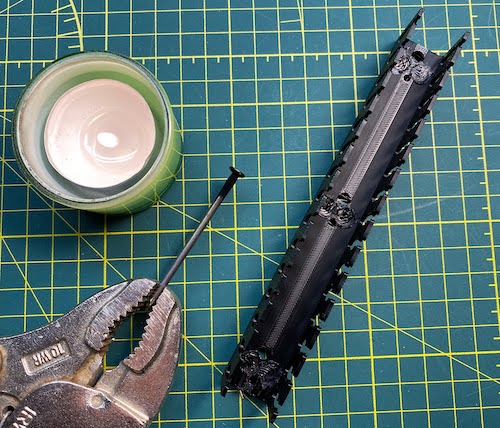
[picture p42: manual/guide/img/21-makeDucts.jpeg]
      \
      *fig 21.1*

2. Add JST-XH connectors to the sensors/probes/switches/steppers/MOSFET
   1. For the BLTouch you need a female 3 pin connector for the servo control (Brown=GND, Red=+5V, Orange=Signal) and a female 2 pin connector for the switch (Black=GND, White=Z-min).

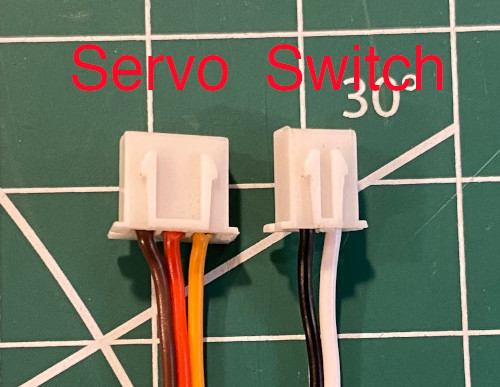
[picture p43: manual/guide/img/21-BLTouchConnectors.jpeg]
      \
      *fig 21.2*

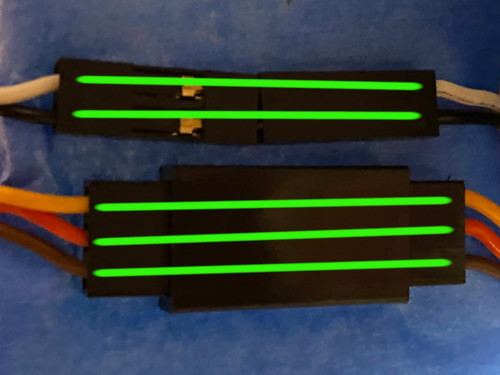
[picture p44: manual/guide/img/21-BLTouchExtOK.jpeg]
      \
      *fig 21.3*
   
      *Note: If you bought the BLTouch wire extension cable, make sure they didn't switch the wires in the connector. I had this problem!!*

   3. For the hotend and heated bed thermistors you need female 2 pin connectors. Polarity doesn't matter.

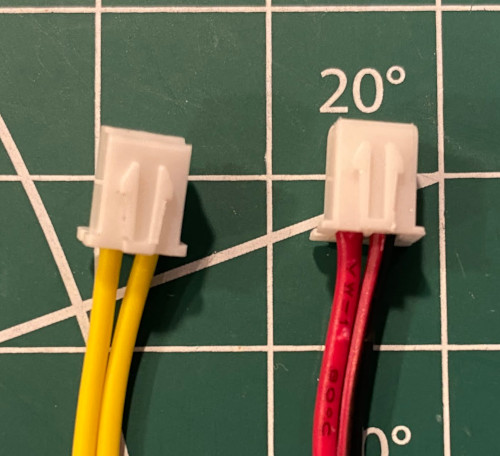
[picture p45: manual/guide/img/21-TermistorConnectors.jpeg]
      \
      *fig 21.4*
   4. For the fans and MOSFET control wire you need female 2 pin connectors.

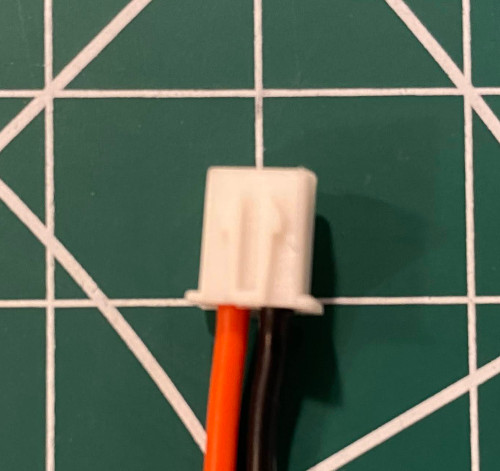
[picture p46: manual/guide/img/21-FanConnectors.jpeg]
      \
      *fig 21.5*

   5. For the switches you need female 3 pin connectors.

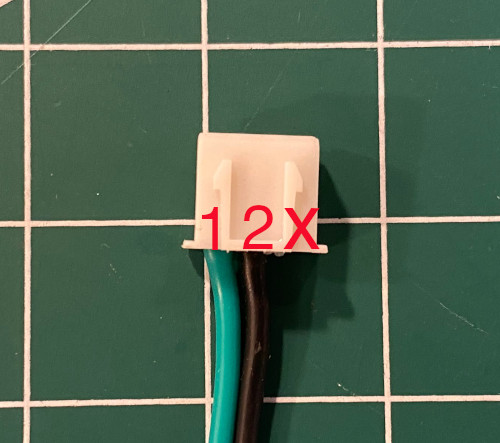
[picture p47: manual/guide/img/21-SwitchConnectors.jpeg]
      \
      *fig 21.6*
   6. For stepper motors you need female 4 pin connectors.

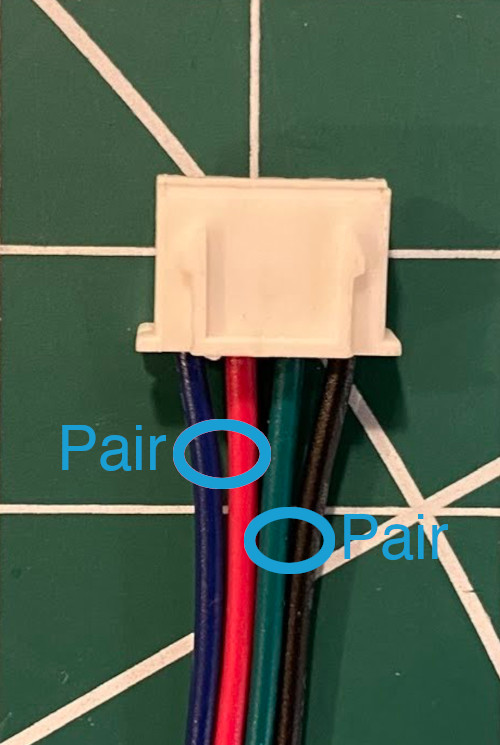
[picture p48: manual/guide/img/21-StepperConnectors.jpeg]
      \
      *fig 21.7*

      Note: Not all stepper motors use the same color codes. This is the correct sequence for [SKR boards](img/21-BTT_SKR_V1.4PIN.pdf) and [StepperOnline stepper motors](img/21-17HS19-2004S1.pdf).
      Only thing that matters is that the coil pairs be grouped together ([Finding Stepper Pairs](https://3ddistributed.com/duet-wifi/stepper-motor-wire-color-and-coil-pairs/))
  
   7. Here is the list of JST-XH connectors you should have when you are done:
      
| Description | No. of</BR> Pins | Gender |
|---|---|---|
| BLTouch Servo | 3 | Female |
| BLTouch Switch | 2 | Female |
| Hotend Thermistor | 2 | Female |
| Heated Bed Thermistor  | 2 | Female |
| Hotend Fan | 2 | Female |
| Control Board Fan | 2 | Female |
| Parts Cooling Fan | 2 | Female |
| X Endstop Switch | 2 | Female |
| Y Endstop Switch | 2 | Female |
| Left Stepper Motor | 4 | Female |
| Right Stepper Motor | 4 | Female |
| Z1 Stepper Motor | 4 | Female |
| Z2 Stepper Motor | 4 | Female |
| Extruder Stepper Motor | 4 | Female |
| MOSFET Control | 2 | Female |

3. Install heat sinks onto TMC2208 stepper drivers. Make sure heat sink doesn't short any of the pins.

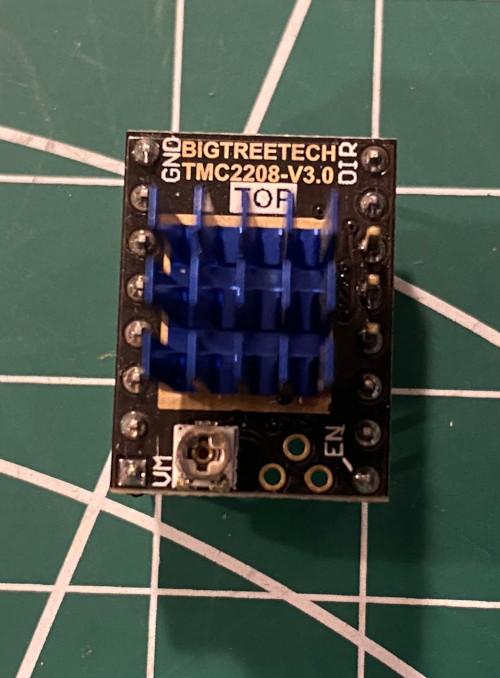
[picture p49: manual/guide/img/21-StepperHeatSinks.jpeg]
   \
   *fig 21.8*

4. Using a sharpie color the negative terminals on the controller board [SKR 1.4 board pinout](img/21-BTT_SKR_V1.4PIN.pdf). 

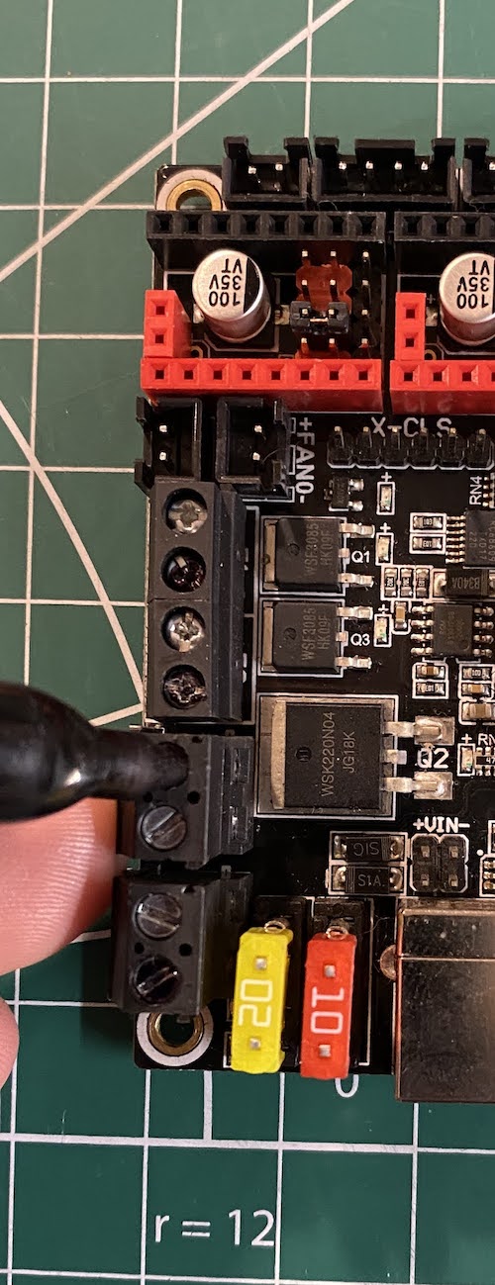
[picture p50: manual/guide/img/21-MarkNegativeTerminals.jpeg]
   \
   *fig 21.9*

### Assembly
1. Set the jumpers on the controller board [SKR 1.4 Manual](img/BTT SKR V1.4 Instruction Manual.pdf).

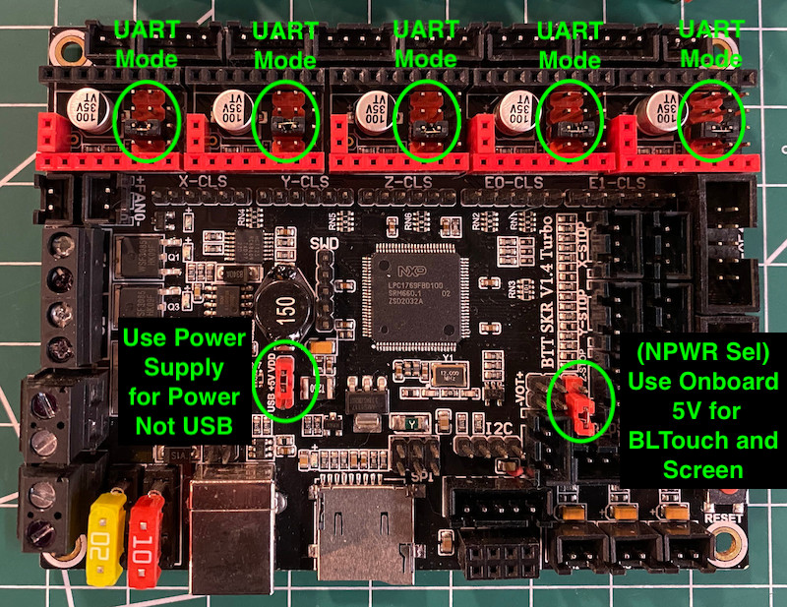
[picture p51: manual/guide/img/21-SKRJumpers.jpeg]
   \
   *fig 21.10*

2. Install the TMC2208 stepper drivers on the control board.

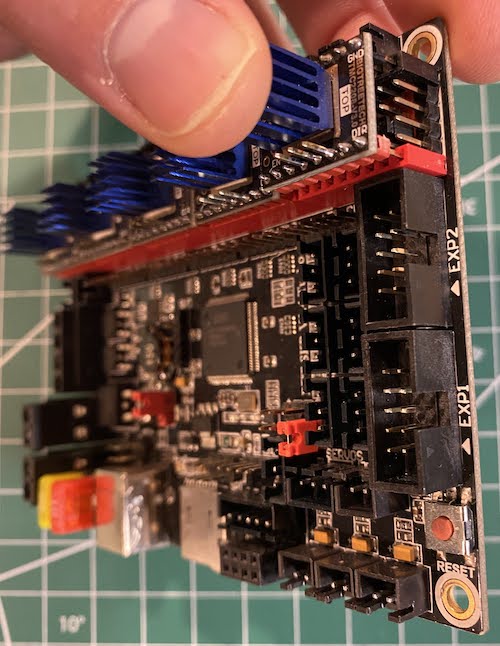
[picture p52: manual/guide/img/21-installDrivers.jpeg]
   \
   *fig 21.11*

3. Draw guidelines for slotted wire ducts.

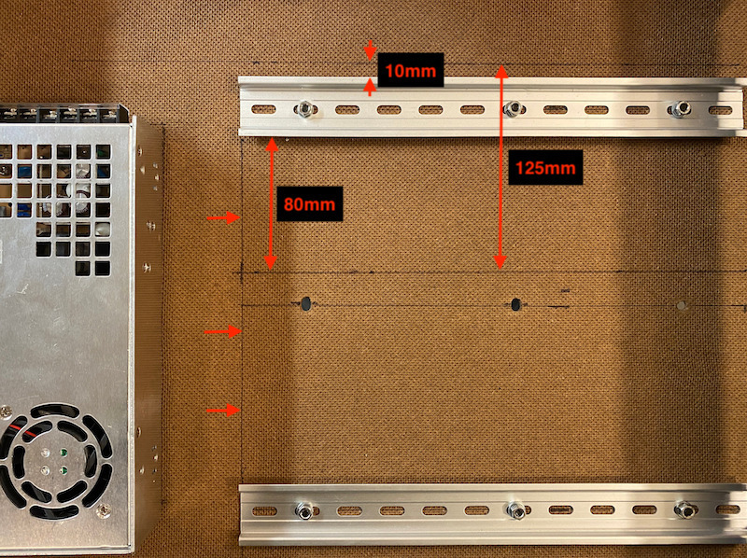
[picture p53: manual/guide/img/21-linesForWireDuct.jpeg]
   \
   *fig 21.12*
4. Remove the electronics panel and mark M3 mounting holes, using the slotted wiring ducts as a template. Note I only did 2 mounting holes per duct.

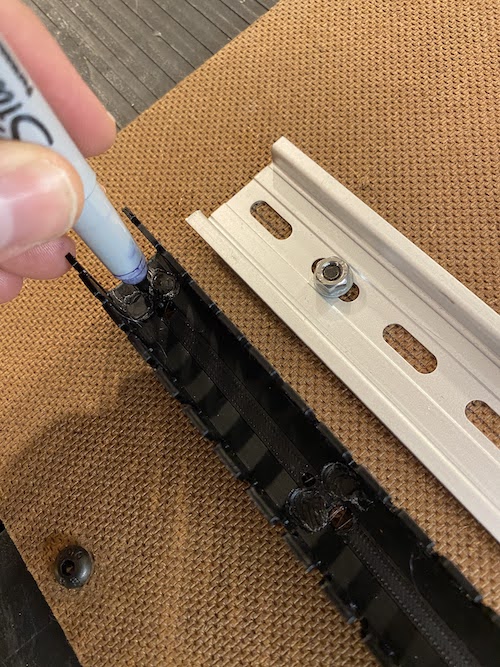
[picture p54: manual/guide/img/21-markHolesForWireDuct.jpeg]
   \
   *fig 21.13*

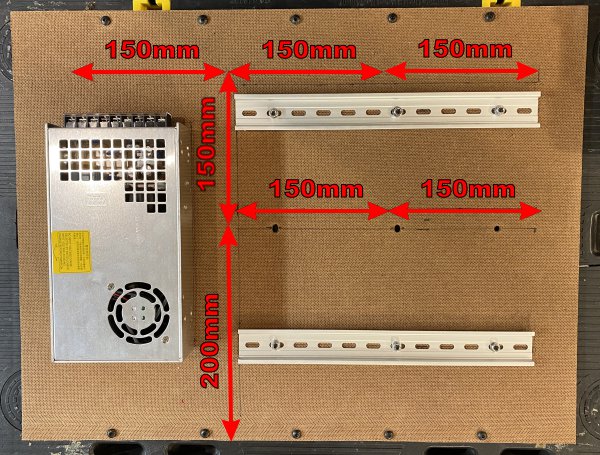
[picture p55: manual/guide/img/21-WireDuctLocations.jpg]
    \
    *fig 21.14*

5. Drill holes for ducts using a 1/8" or 3.2mm drill bit. Clean up and widen any holes that need adjusting with an X-acto knife.

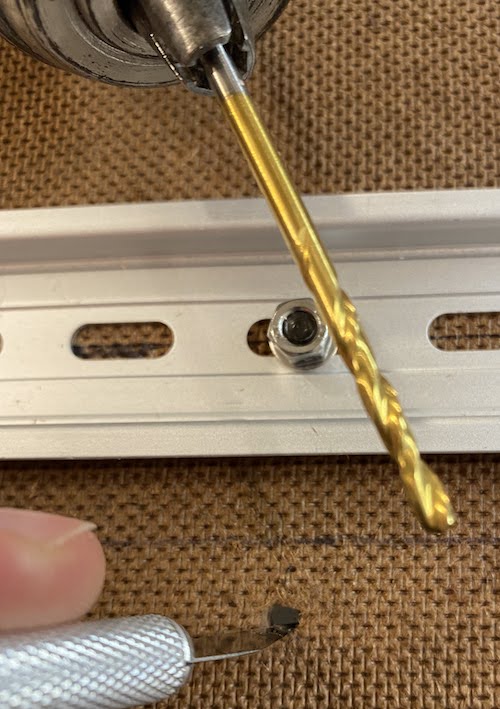
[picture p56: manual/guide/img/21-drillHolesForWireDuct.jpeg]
   \
   *fig 21.15*

6. Mount ducts using 2 10mm M3 bolts, washers, and nuts each. Washers are between the bolt head and hardboard.

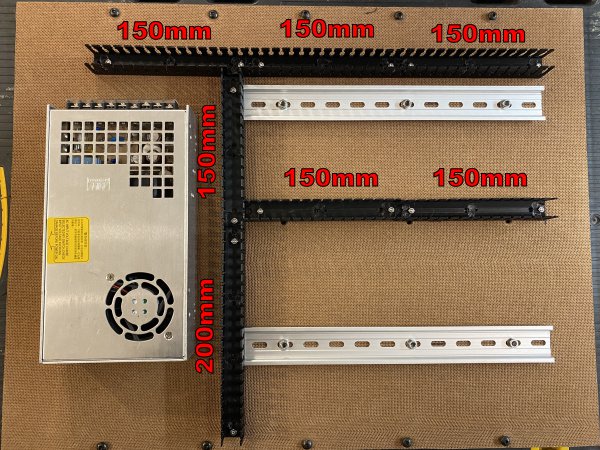
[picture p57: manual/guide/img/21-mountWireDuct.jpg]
   \
   *fig 21.16*
7. Break off slotted wiring duct fingers where the ducts intersect.

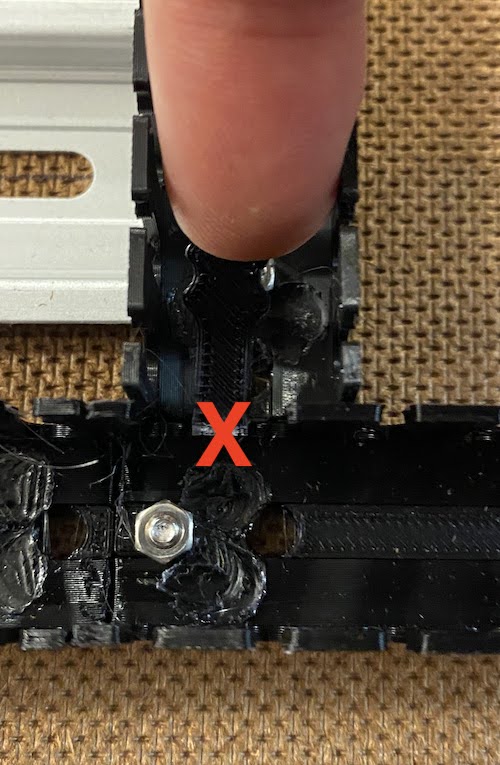
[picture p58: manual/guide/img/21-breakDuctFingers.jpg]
   \
   *fig 21.17*

8. Reinstall the electronics panel

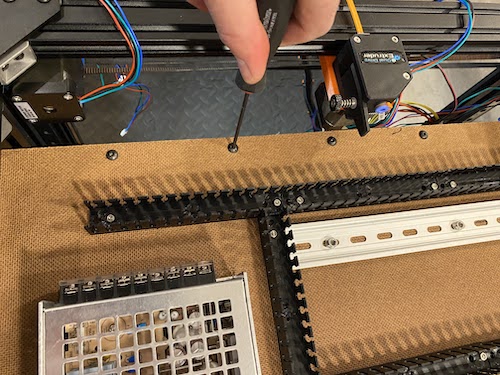
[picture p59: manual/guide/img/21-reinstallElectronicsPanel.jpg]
   \
   *fig 21.18*

9. Mount the controller board to the DIN rails using the 3d printed mounts. To make room for the USB cable you will need to remove one of the wiring duct fingers (Fig 21.20).

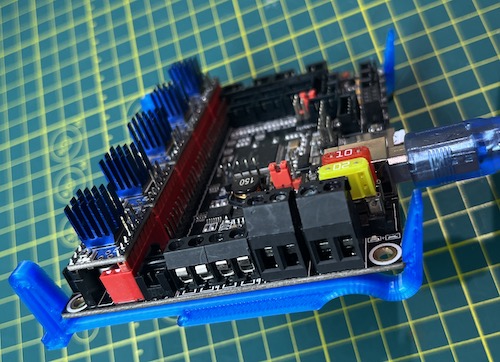
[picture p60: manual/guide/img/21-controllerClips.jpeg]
   \
   *fig 21.19*

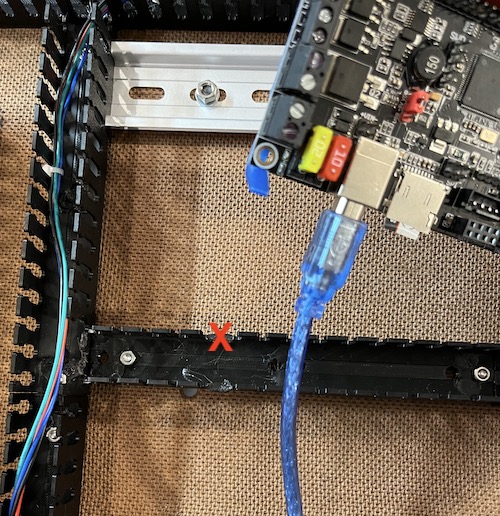
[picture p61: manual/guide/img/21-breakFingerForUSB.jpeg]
   \
   *fig 21.20*

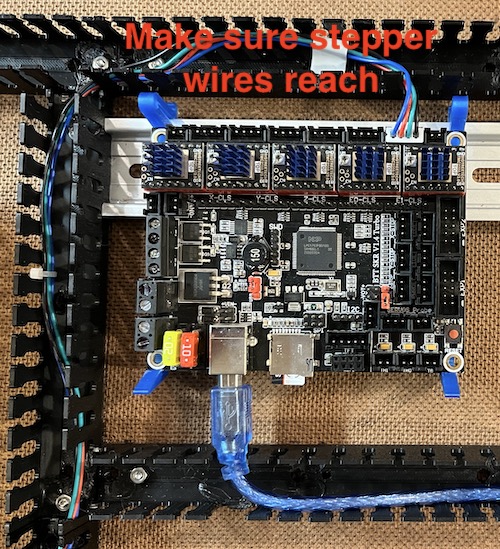
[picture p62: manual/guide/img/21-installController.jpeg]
   \
   *fig 21.21*

    Note: Verify that all the stepper wires can reach.

10. Attach 4010 fan to the 3d printed 4010 DIN Mount using 2x M3 16mm screws and nuts.

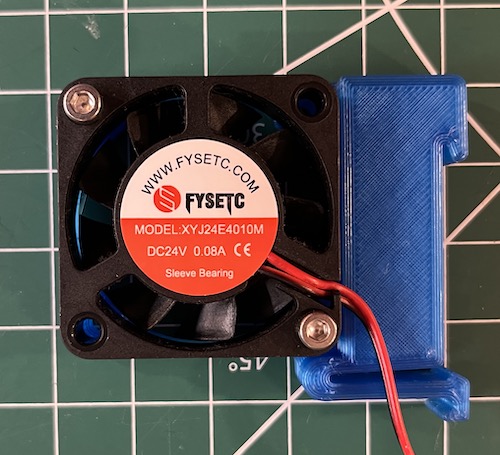
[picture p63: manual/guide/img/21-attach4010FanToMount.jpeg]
    \
    *fig 21.22*

11. Install the 4010 fan, MOSFET, and Raspberry Pi to the DIN rails using the corresponding 3d printed mounts.

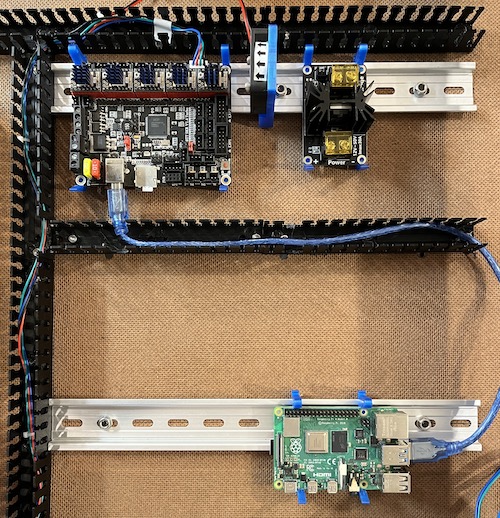
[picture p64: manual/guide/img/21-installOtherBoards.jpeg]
    \
    *fig 21.23*

12. Connect the power supply to the controller board and MOSFET using the 14AWG red and black primary wire. Make sure to use stranded wire with at least 14 AWG.

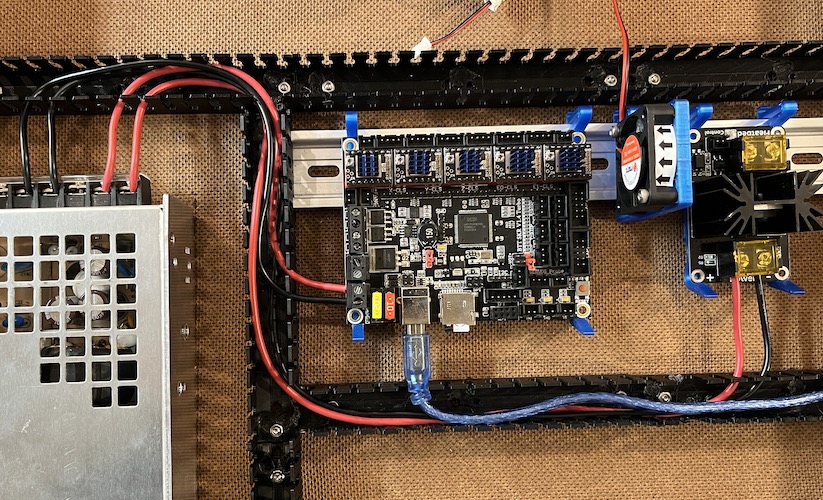
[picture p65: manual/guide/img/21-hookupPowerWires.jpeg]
    \
    *fig 21.24*

13. Connect all electrical components to the controller board and MOSFET as indicated in this wiring diagram

    \
    *fig 21.25*

14. Using 5 of the vertical wire mounts secure the TFT touch screen cables with the zip ties.

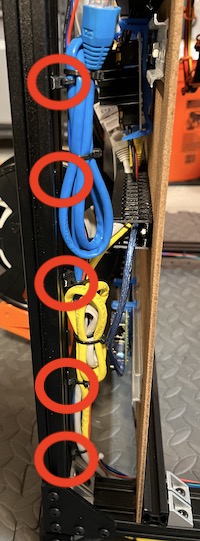
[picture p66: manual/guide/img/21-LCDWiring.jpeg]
    \
    *fig 21.26*

15. This is what it should look like with everything wired up.

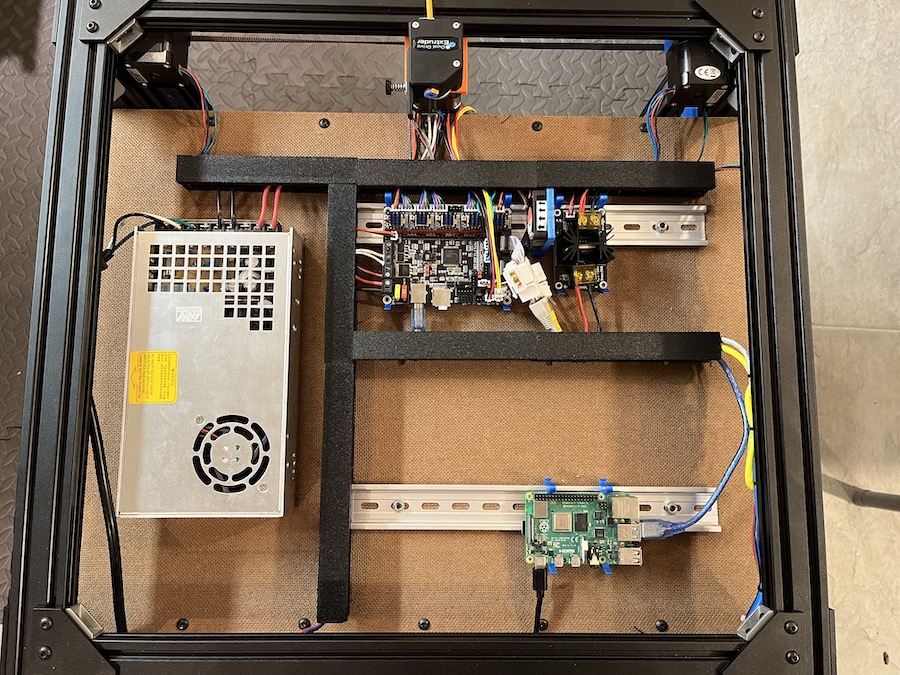
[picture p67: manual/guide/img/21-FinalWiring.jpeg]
    \
    *fig 21.27*

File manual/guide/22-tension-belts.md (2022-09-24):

# My BLV MGN Cube - Step 22 Tension Belts

## [Step 22 BoM Spreadsheet Link](https://docs.google.com/spreadsheets/d/e/2PACX-1vTVx7BvB3V7CozF2l4eWkNntWrHSjOawmrsi_bRSVxQLIGVlfZTYEGp8a6fHpENV6hV2cn9PrDLHHl0/pubhtml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)

### Procedure
1. Attach the bottle weight to the tension tool using the wire. The bottle weight should be able to pivot freely.

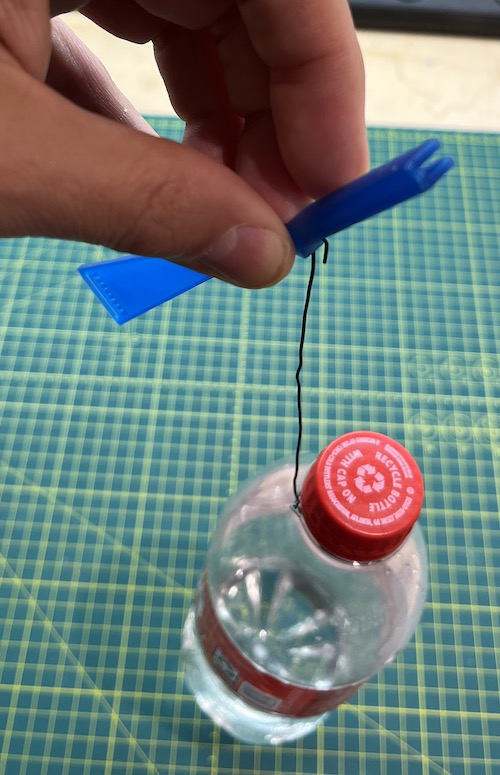
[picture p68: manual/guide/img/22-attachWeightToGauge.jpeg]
   \
   *fig 22.1*

2. With everything on the kitchen scale add water to the bottle so that the entire tool weighs 200g. You can use the spray bottle to add water in small amounts for fine-tuning.

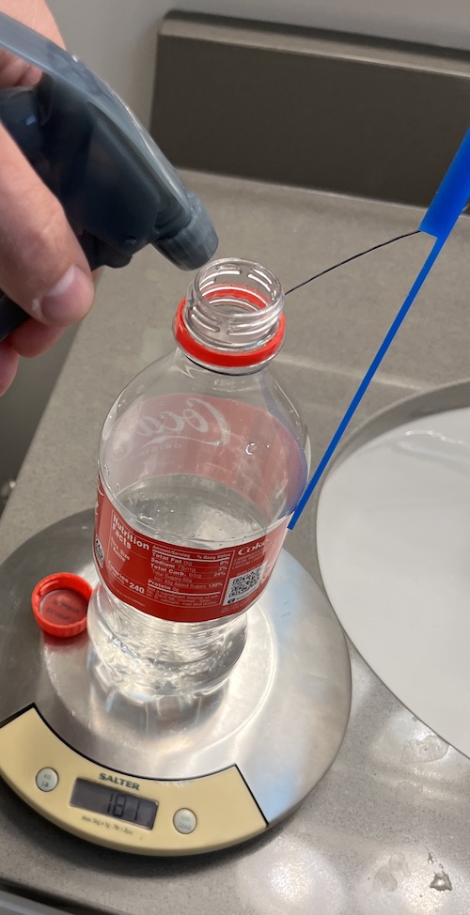
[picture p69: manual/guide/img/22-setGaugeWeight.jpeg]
   \
   *fig 22.2*

3. Lock the X gantry against the front idler holders using the 2x 2020 jigs, M5 10mm screws, and T-nuts.

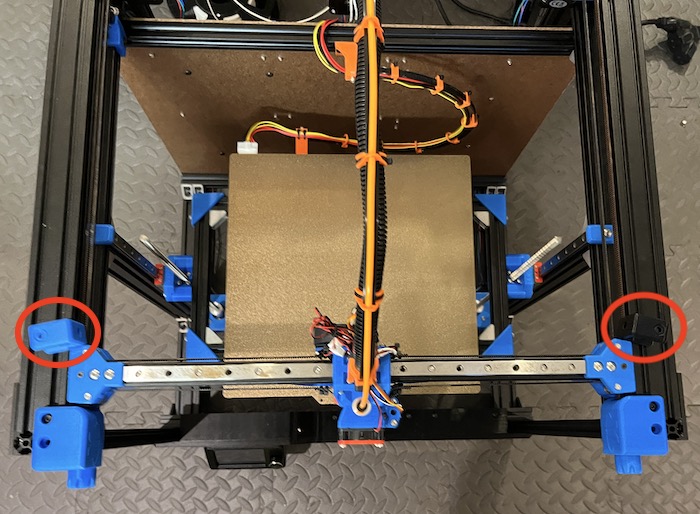
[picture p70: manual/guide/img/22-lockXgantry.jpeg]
   \
   *fig 22.3*

4. Center the X carriage on the X gantry and lock it in pace with the 2x X carriage clamps, M5 x 10mm screws, and T-nuts.

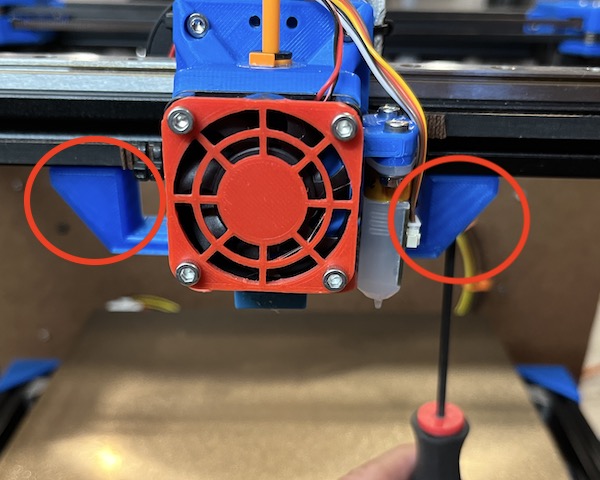
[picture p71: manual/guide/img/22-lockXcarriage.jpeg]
   \
   *fig 22.4*

5. Find and mark the center line for the left side and right side of the belts. Measure from the pulleys in the back corner blocks to the corresponding pulleys in the X gantry.

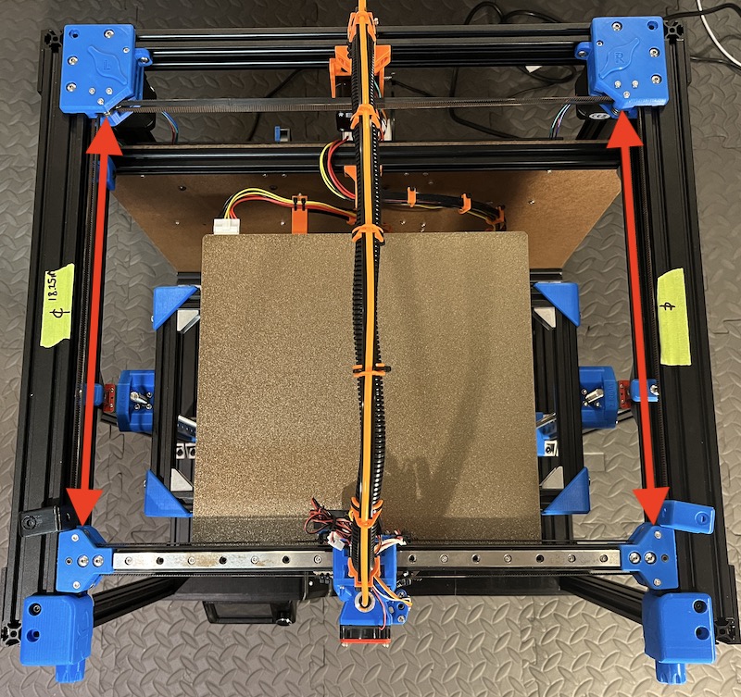
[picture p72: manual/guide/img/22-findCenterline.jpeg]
   \
   *fig 22.5*

6. Put the printer on its left side and attach the gauge to the belt making sure to align the pivot with the center line.

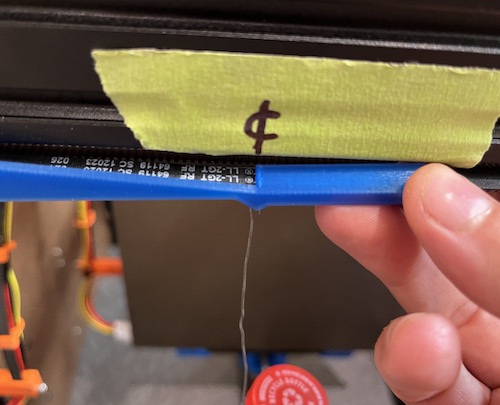
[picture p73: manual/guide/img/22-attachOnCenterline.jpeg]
   \
   *fig 22.6*

7. Adjust the front tensioner so the belt is visible through the middle hole on the tool.

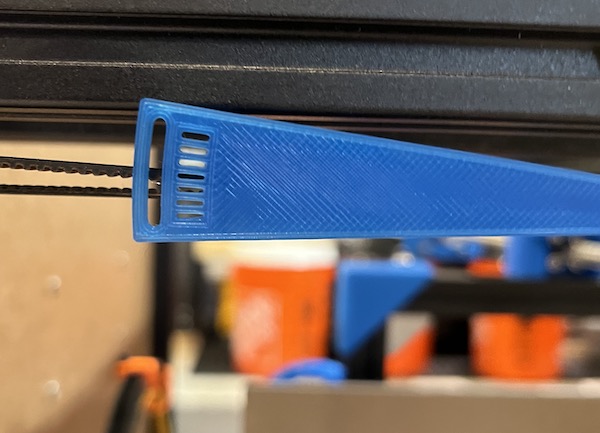
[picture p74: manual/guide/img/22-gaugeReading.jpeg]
   \
   *fig 22.7*

8. Repeat steps 6 through 8 for the printer on its right side.

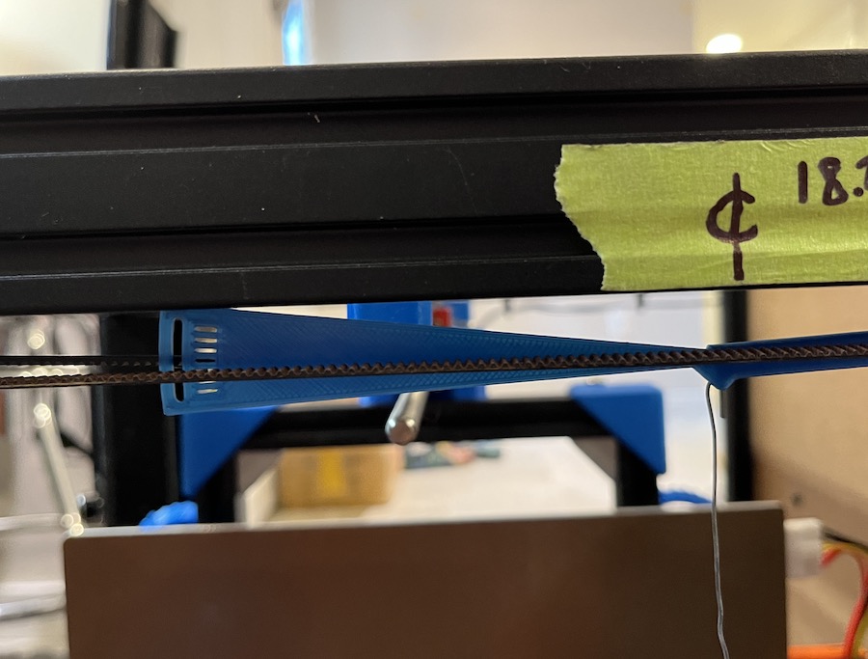
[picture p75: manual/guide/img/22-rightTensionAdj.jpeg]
   \
   *fig 22.8*

9. Remove the X gantry and X carriage locks.

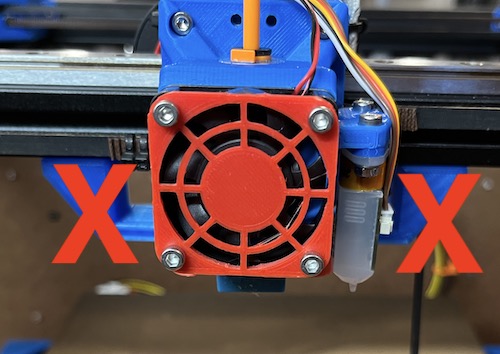
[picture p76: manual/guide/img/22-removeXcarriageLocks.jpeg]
   \
   *fig 22.9*

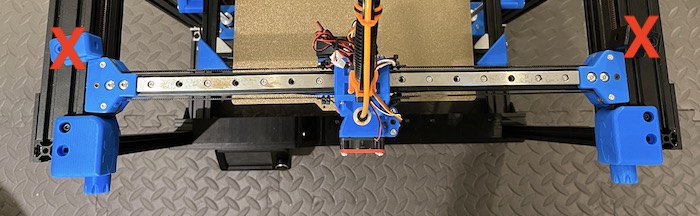
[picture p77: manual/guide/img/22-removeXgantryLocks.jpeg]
   \
   *fig 22.10*

11. Verify the X gantry is square.
    1. Manually move the X gantry from each side to contact the front idler blocks. There should be no gap on the alternate block.

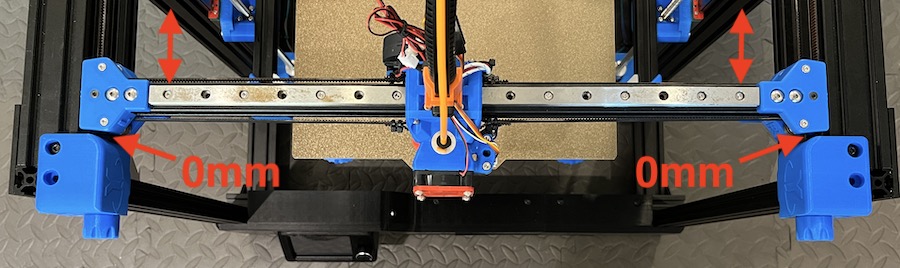
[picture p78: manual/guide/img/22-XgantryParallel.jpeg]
        \
        *fig 22.11*

    2. If it isn't parallel then alternately loosen one tensioner while tightening the other the exact same amount. This will allow you to adjust for any minor asymmetry while still keeping the belt tension uniform.

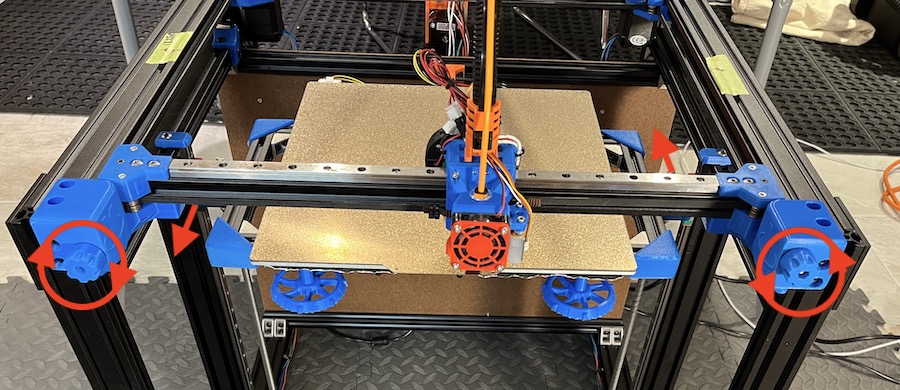
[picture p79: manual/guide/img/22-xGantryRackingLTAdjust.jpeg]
        \
        *fig 22.12*
    
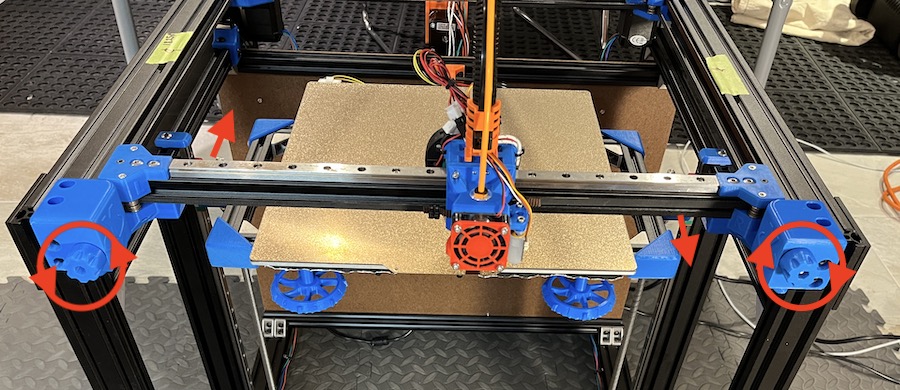
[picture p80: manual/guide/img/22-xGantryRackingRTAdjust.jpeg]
        \
        *fig 22.13*

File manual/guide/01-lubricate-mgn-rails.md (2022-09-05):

# My BLV MGN Cube - Step 1 Lubricate MGN Rails

### Checkout my Comparison of Several Reasonably Priced Linear Rail Brands

[Linear Rail Bake-off](../../notes/linear-rail-bakeoff.md)

## [Step 1 BoM Spreadsheet Link](https://docs.google.com/spreadsheets/d/e/2PACX-1vTVx7BvB3V7CozF2l4eWkNntWrHSjOawmrsi_bRSVxQLIGVlfZTYEGp8a6fHpENV6hV2cn9PrDLHHl0/pubhtml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)

### Prep

1. Tape some magnets to the bottom of a mason jar.

    \
    *fig 1.1*

1. Tape some magnets to the bottom of the large container.

    \
    *fig 1.2*

3. Put a shop towel in the bottom of the large container.

    \
    *fig 1.3*

4. Put the alcohol in a mason jar.

    \
    *fig 1.4*

## Procedure

**DO ONE RAIL AT A TIME AND DON'T INTERMIX PARTS**

1. Remove the plug from one end of rail. I used a small allen key on the other side of the rail. Save the plug for later.

    \
    *fig 1.5*

2. Carefully slide carriage off of rail, over large container. The bearings can pop out of the carriage when removing it from the rail.

    \
    *fig 1.6*

3. Dab a shop towel in the alcohol and wipe down the rail removing any anti rust gunk the factory put on.

    \
    *fig 1.7*

4. Repeat by using a alcohol soaked pipe cleaner to thoroughly clean the races.

    \
    *fig 1.8*

5. Use the spray air to quickly dry the alcohol off the rail and remove any lint.

    \
    *fig 1.9*

6. Spray the rail with silicone lubricant and wipe off excess. Do this outside or over a utility sink cause it's messy. Also wear some disposable gloves.

    \
    *fig 1.10*

7. Set the rail aside to dry. Oh and put on a fresh set of gloves.

8. Disassemble the carriage over a mason jar and in the large container.

    1. Unscrew the dust cap. Yeah I should have done this in the mason jar as well.

        \
        *fig 1.11*

    2. Carefully remove the bearing retainer wires using an X-Acto knife or something sharp. Be careful not to bend the wires. They're delicate.
       **Bearings WILL fall out here so do this and the rest of the dissembly steps in a jar inside the container**

        \
        *fig 1.12*

    3. Pry off the end caps and separate into 2 halves. Also empty the remaining ball bearings into the jar.

        \
        *fig 1.13*

    4. Here is what the Carriage should look like fully disassembled.

        \
        *fig 1.14*

9. Degrease all the carriage parts.
    1. Degrease the main carriage body in the mason jar filled with alcohol. Use a pipe cleaner soaked in alcohol to clean the ball return holes.

        \
        *fig 1.15*

    2. Degrease the rest of the parts in the alcohol jar and using the pipe cleaners soaked in alcohol. Retaining Wires/Dust Covers/Plastic End Caps. Don't do the ball bearings just yet.

        \
        *fig 1.16*

        \
        *fig 1.17*

        \
        *fig 1.18*

    3. Carefully put the ball bearings in a shallow dish/plastic cap etc... and pour alcohol over them. **Don't use the 2 part mason jar lid**

        \
        *fig 1.19*

10. Dry all the carriage parts.
    1. Using the spray air dry the carriage. Especially the ball return and screw holes.

        \
        *fig 1.20*

    2. Using the spray air dry the Plastic End Caps.

        \
        *fig 1.21*

    3. Slowly pour off the alcohol from the cap containing the bearings into the mason jar. And on a paper towel, in the large container dump the bearings. Roll them in the paper towel to dry them.

        \
        *fig 1.22*

    4. Dry off the wires and Dust covers.

11. Reassemble the Carriage without the bearings.

    \
    *fig 1.23*

12. Add the bearings into the carriage races using tweezers. Use your fingers to pop them into the races. Insert bearings (33) into each side until it looks like there is only one space left.

    \
    *fig 1.24*

    \
    *fig 1.25*

    \
    *fig 1.26*

13. Put oil on the bearings. I normally do 5 drops per side.

    \
    *fig 1.27*

14. Put the carriage back on the rail. Be careful as bearings tend to pop out.

    \
    *fig 1.28*

15. Put some oil in the hole in the center of both end caps. This will crate a little reserve of oil for the bearings.

    \
    *fig 1.29*

16. Use zip ties to secure the ends of the rails so the carriage doesn't accidentally slip off.

    \
    *fig 1.30*

17. Now run the carriage back and forth to work the oil into the bearings. To test slowly move the carriage and check for binding. It probably wont be perfect. Perfect = $200. I've also noticed they get smoother after the oil has had a day or 2 to penetrate.

### References

https://clevercreations.eu/clean-repair-linear-guide-rails/

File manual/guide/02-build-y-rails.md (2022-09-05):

# My BLV MGN Cube - Step 2 Build Y Rails

### [Step 2 BoM Spreadsheet Link](https://docs.google.com/spreadsheets/d/e/2PACX-1vTVx7BvB3V7CozF2l4eWkNntWrHSjOawmrsi_bRSVxQLIGVlfZTYEGp8a6fHpENV6hV2cn9PrDLHHl0/pubhtml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)

#### Assembly

1. Attach T-Nuts into every other hole of linear rail using M3 8mm socket head cap screws. If there is an extra hole just double up at the end. Be careful not to let the carriages fall off the linear rails.

    \
    *fig 1.1*

2. Mount a rail on one of the 2040 extrusions and center over the left channel using the two 2040 jigs to properly center it.

    \
    *fig 1.2*

3. If your jigs are a little loose you can use some tape placed equally on both sides to tighten them up (See Fig 1.2 and Fig 1.3).

    \
    *fig 1.3*

4. Offset the top of the rail by 70mm. This is because the pulleys at the back of the printer take up more space than the tensioner at the front.

    \
    *fig 1.4*

5. Tighten the T-Nuts using the guides to make sure the linear rail remains centered over the channel.

    \
    *fig 1.5*

6. Repeat the above steps to complete the right rail.

7. Here is what it should look like when you are done.

    \
    *fig 1.6*

[Next Step](03-frame-sides.md)

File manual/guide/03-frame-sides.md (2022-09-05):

# My BLV MGN Cube - Step 3 Build Frame Sides

## [Step 3 BoM Spreadsheet Link](https://docs.google.com/spreadsheets/d/e/2PACX-1vTVx7BvB3V7CozF2l4eWkNntWrHSjOawmrsi_bRSVxQLIGVlfZTYEGp8a6fHpENV6hV2cn9PrDLHHl0/pubhtml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)

### Prep

1. Measure brackets and find 4 that are close to 20mm on one side. Might have to file them down or add a little tape. You'll use these to correctly position your first joint so the closer to 20mm the better. Mark these 4 brackets with a Sharpie.

    \
    *fig 2.1*

3. Find a the flattest surface in your house. Hint, If you have a granite counter top that's probably the best. Make sure it's clean and then use one of your pieces of extrusion as a straight edge and a piece of paper as a thickness gauge. Try and slip a piece of paper under the extrusion in a couple of places to test for flatness. Test multiple directions. Probably won't be perfect but pick the best counter you have. This will be the surface you use to build the frame.

    \
    *fig 2.3*

4. Check extrusion ends for squareness. We'll be relying on the extrusion ends being square to produce a square frame. The kits should all have pretty good cuts. To check for squareness, but two ends against each other (you should only see a hairline crack where they meet. Flip one around and check it the other way. If you have the same result you're good! If they aren't cut perfectly square or aren't to exact length it's going to be a challenge to get a square frame.

    \
    *fig 2.4*

5. Cover the surface in a large piece of craft paper to protect it. *Can't build a 3d printer if your significant other murders you for scratching their counter top with sharp edged extrusions*

### Assembly - Left Side

1. Arrange the spare extrusions, mentioned in the tools section, in a diamond. These will support the frame and keep it level even with the rails and the printed parts mounted on them.

    \
    *fig 2.6*

2. Attach M5 bolts and T-nuts to the 4 plates and lay out the extrusions with the plates installed but not tightened. Also now is the time to position the tensioner mount (Circled in fig 2.10). Don't forget the M5 bolts/T-nuts for the tensioner mount (fig 2.8). Note one hole on the tensioner mount should remain empty (fig 2.7). Insert the top and right extrusions through the tensioner, but keep the tensioner's bolts loose (fig 2.9).

    \
    *fig 2.7*

    \
    *fig 2.8*

    \
    *fig 2.9*

    \
    *fig 2.10*

3. Mount 2 of the 20mm lower brackets, that you prepared earlier, flush with the bottom of the extrusion. You can use one of the other pieces of extrusion to help with this, see fig 2.11. This will be used to make sure the 496mm extrusion is inset exactly 20mm when attached to the 560mm extrusions. Tighten to the 560mm extrusion while keeping them snug with the bottom ledge in the foot cutout. Repeat for the other lower corner. **_Ignore the blue feet in these pictures, I've moved that to a later step_**

    \
    *fig 2.11*

    \
    *fig 2.12*

5. Compress the bottom of the frame *gently* using bar clamp or your helper. Make sure the top of the frame extrusions don't have gaps. This will ensure things are pretty square. **DONT OVER TIGHTEN THE CLAMPS!! YOU CAN BEND THE EXTRUSION**

    \
    *fig 2.13*

6. Now check that things are fairly square, finish attaching the 4 lower brackets to the horizontal 496mm extrusion. All extrusions should butt up to one another and be flush. *We're trusting the extrusion ends to be square so don't worry if there is a little wiggle when checking the angle. We're just making sure things aren't grossly out of alignment*

    \
    *fig 2.14*

7. Attach the 2 bottom plates. First finger tight and then use the tightening sequence in the figure.

    \
    *fig 2.15*

8. This is what you should have when you are done. *Make sure all both bottom joints are flush*

    \
    *fig 2.16*

10. On the top attach the 2 extra plates, mentioned in the tools list, to the top extrusion. These will help make sure you attach the extrusions flush with the top. *Also see fig 2.18*

    \
    *fig 2.17*

11. Compress the top of the frame *gently* using bar clamp or your helper. This will ensure things are pretty square/tight/flush. **DONT OVER TIGHTEN THE CLAMPS!! YOU CAN BEND THE EXTRUSION**

    \
    *fig 2.18*

12. Now tighten plates while making sure the 2x 496mm extrusions are flush with the top extrusion with the linear rail. *This is why we have those extra plates attached to the top*

    \
    *fig 2.19*

    \
    *fig 2.19*

13. Remove the plates from the top rail, that you used for alignment. Check all joints. There should be no gaps anywhere

    \
    *fig 2.20*

14. Now install the remaining brackets in all the corners. *There is only one bracket in the corner with the tensioner*

    \
    *fig 2.20*

    \
    *fig 2.21*

15. Tighten down the tensioner bolts.

    \
    *fig 2.22*

16. Install the Left bottom x mount.

    \
    *fig 2.23*

17. Here is the final product.

    \
    *fig 2.23*

### Assembly - Right Side
1. Using the printed parts for the right side repeat the [Assembly - Left Side](#assembly---left-side) procedure to build the right side. It should be a mirror image of the left side.
2. One difference is that 12 brackets are used instead of 11. The corner with the tensioner takes 2 brackets for the right side.

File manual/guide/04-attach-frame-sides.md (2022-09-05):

# My BLV MGN Cube - Step 4 Attach Frame Sides

## [Step 4 BoM Spreadsheet Link](https://docs.google.com/spreadsheets/d/e/2PACX-1vTVx7BvB3V7CozF2l4eWkNntWrHSjOawmrsi_bRSVxQLIGVlfZTYEGp8a6fHpENV6hV2cn9PrDLHHl0/pubhtml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)

### Prep
1. Install 3x M5 10mm bolts and T-nuts on each frame foot and attach some felt to prevent scratches.

    \
    *fig 4.1*

2. Measure brackets and find 4 that are close to 20mm on one side. Might have to file them down or add a little tape. You'll use these to correctly position your first joint so the closer to 20mm the better. Mark these 4 brackets with a Sharpie.

    \
    *fig 4.2*

3. Find a the flattest surfance in your house. Hint, If you have a granite counter top that's probably the best. Make sure it's clean and then use one of your pieces of extrusion as a straight edge and a piece of paper as a thickness guage. Try and slip a piece of paper under the extrusion in a couple of places to test for flatness. Test multiple directions. Probably won't be perfect but pick the best counter you have. This will be the surface you use to build the frame.

    \
    *fig 4.3*

4. Check extrusion ends for squareness. We'll be relying on the extrusion ends being square to produce a square frame. The kits should all have pretty good cuts. To check for squareness, but two ends against each other (you should only see a hairline crack where they meet. Flip one around and check it the other way. If you have the same result you're good! If they aren't cut perfectly square or aren't to exact length it's going to be a challenge to get a square frame.

    \
    *fig 4.4*

5. Cover the surface in a large piece of craft paper to protect it. *Can't build a 3d printer if your significant other murders you for scratching their counter top with sharp edged extrusions*

### Assembly

1. Flush mount 1 bracket on each leg of the left frame side. *Will be used to attach the cross members*

    \
    *fig 4.5*

    \
    *fig 4.6*

2. Attach 1st cross member using the bar clap to keep it flush against frame side. Attach one of the plates and finger tighten the plates and brackets.

    \
    *fig 4.7*

3. Check to make sure the cross member is square. Check multiple angles. It's fairly important to make sure its square as well as flush because you don't want to build tension in and possibly rack the cube at this point.

    \
    *fig 4.8*

4. Now that the cross member is square tighten down the plate and bracket in the following sequence

    \
    *fig 4.9*

5. Now that the 1st cross member is done, repeat for the steps above for other lower cross member.

    \
    *fig 4.10*

6. Now lets move to the upper back crossmember. This is the corner without the tensioner. Temporarily attach one plate to the top rail to help with aligning the crossmember and attach another plate to the left side back extrusion.

    \
    *fig 4.11*

7. Now attach the last cross member and make sure it is square before tightening down only the back plate.

    \
    *fig 4.12*

8. Add 2 brackets to reinforce the cross member and then put the left side and crossmembers on the floor. Shim up a corner to keep it from rocking.

    \
    *fig 4.13*

9. Remove the helper plate.

    \
    *fig 4.14*

10. Here's what it should look like at this point.

    \
    *fig 4.15*

11. Flush mount 1 bracket on each leg of the right frame side. You shoud tighten these down. *Will be used to attach the cross members*

    \
    *fig 4.16*

    \
    *fig 4.17*

12. Carefully place the right side on top of the cross members and finger tighten the leg brackets to the cross members. * You'll be using the brackets and legs together to make everything flush*

    \
    *fig 4.18*

13. Attach the plates that connect Right side to cross members. Try and keep things flush). *Note the pate attaches the the 2040 channel closest to the cross member and not the one closest to the other plate*

    \
    *fig 4.19*

14. Now tighten everything down making sure to keep everything as flush and square as possible. *I had to slightly adjust one cross member that didn't line up. I loosened as few bolts as possible and moved it closer. Still wasn't perfect but good enough.*

15. Now go around and add any missing brackets. This is what it should look like when it's done. Now would be a good time to measure and verify angles as well. **One more step after the pictures**

    \
    *fig 4.20*

    \
    *fig 4.21*

    \
    *fig 4.22*

    \
    *fig 4.23*

    \
    *fig 4.24*

16. Last add the feet.

    \
    *fig 4.25*

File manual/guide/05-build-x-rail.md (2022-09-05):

# My BLV MGN Cube - Step 5 Build X Rail

## [Step 5 BoM Spreadsheet Link](https://docs.google.com/spreadsheets/d/e/2PACX-1vTVx7BvB3V7CozF2l4eWkNntWrHSjOawmrsi_bRSVxQLIGVlfZTYEGp8a6fHpENV6hV2cn9PrDLHHl0/pubhtml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)

### Prep
1. Install M5 8mm screws and T-nuts in the top blocks.

    \
    *fig 5.1*

2. Clean the nut traps and holes on the lower blocks using the needle files.

    \
    *fig 5.2*

    \
    *fig 5.3*

### Assembly

1. Attach M5 16mm screws and M5 8mm screws with T-Nuts to both left and right lower blocks

    \
    *fig 5.4*

2. Place the 460mm 2020 extrusion on top of the lower blocks. *should be a tight fit but still allow the rails to slide freely*

    \
    *fig 5.5*

3. Use Zip Ties to attach the build plate into the channel of the 2020 extrusion and channel of the back 2040 extrusion. *This is used to keep the 2020 extrusion perfectly parallel to the back 2040 extrusion*

    \
    *fig 5.5*

4. Tighten the lower block M5 10mm Screws and T-Nuts to firmly attach them to the 2020 extrusion. *Do this on both sides*

    \
    *fig 5.6*

5. Prepare the 2 bearing stacks for assembly. You'll be making a sandwich of washers and bearings. (washer->bottom flanged bearing->washer->top flanged bearing->washer)

    \
    *fig 5.7*

6. Insert the 2x M3 35mm screws into the left upper block and assemble the bearing stacks on them. *If you have particularly skinny washers (0.5mm) you should double them to make 1mm*

    \
    *fig 5.8*

7. While holding the bearing stack, flip the left upper block and slide the attached M3 35mm screws into the corresponding holes in the left lower block. **Don't insert M3's all the way as you still need to put nuts in the bottom block nut traps**

    \
    *fig 5.9*

    \
    *fig 5.10*

8. Slide the M3 thin square nuts into the nut traps for the M3 35mm screws and then tighten them until they catch the nuts. Also insert the M3 50mm screw in the center hole. *Don't tighten any of the screws all the way down yet.

    \
    *fig 5.11*

9. Tighten M5 10mm and M5 16mm screws and T-Nuts in the left upper block into the 2020 extrusion.

    \
    *fig 5.12*

10. Attach the M3 lock nut to the bottom of the M3 50mm screw and tighten it along with the 2x M3 35mm screws.

    \
    *fig 5.13*

13. Repeat the instruction above to complete the right side. *See below for completed view*

    \
    *fig 5.14*

14. Remove build plate you used to keep things square.

    \
    *fig 5.14*

15. Check bearings for free movement. Also check to make sure 2020 extrusion can slide forward and back smoothly on the linear rails. *careful not to slide carriages off of rails*

16. Attach 9x M3 8mm screws and M3 T-Nuts onto the 400mm linear rail.

    \
    *fig 5.15*

17. Install the linear rail onto the top of the 2020 extrusion and attach the 2x 2020 jigs. *make sure the rail is centered between the left and right pulley blocks*

    \
    *fig 5.16*

18. If the 2020 jigs are loose on the 2020 extrusion or allow any play on the linear rail, apply tape to **both** sides of the jig to improve the fit while still keeping it centered. Also make sure to poke a hole so you can tighten the M3 screws with the jig in place.

    \
    *fig 5.17*

19. Starting in the middle of the rail alternate tightening the M3 screws. Work your way to the ends on either side, moving the guides outward and tightening as you go.

    \
    *fig 5.18*

    \
    *fig 5.19*

20. You should now have a perfectly aligned X rail on smoothly sliding y rails.

    \
    *fig 5.20*

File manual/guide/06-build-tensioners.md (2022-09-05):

# My BLV MGN Cube - Step 6 Build Tensioners

## [Step 6 BoM Spreadsheet Link](https://docs.google.com/spreadsheets/d/e/2PACX-1vTVx7BvB3V7CozF2l4eWkNntWrHSjOawmrsi_bRSVxQLIGVlfZTYEGp8a6fHpENV6hV2cn9PrDLHHl0/pubhtml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)

### Assembly

1. Insert M4 into pulley holder.

    \
    *fig 6.1*

2. Partially insert the M3 18mm into the pulley holder.

    \
    *fig 6.2*

3. Slowly add the washer->bearing->washer->bearing->washer into the pulley holder advancing the M3 18mm as you go. You can use some blue tape as a helper. It's a pain. take your time and go slowly.

    \
    *fig 6.3*

    \
    *fig 6.4*

    \
    *fig 6.5*

4. Finish screwing in the M3 18mm until it's flush on both sides of the pulley. Don't worry if it starts splipping because the tensioner body will keep it in place. *This is really just acting as a dowel pin*

    \
    *fig 6.6*

5. Insert the pulley holder into the tensioner body.

    \
    *fig 6.7*

6. Now insert the M4 nut into the adjustment knob and screw onto the end of the m4 bolt. once it bites give it 5 turns.

    \
    *fig 6.8*

    \
    *fig 6.9*

7. Repeat for the right tensioner.

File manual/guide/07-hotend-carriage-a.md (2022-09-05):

# My BLV MGN Cube - Step 7 Partially Build Hotend Carriage

## [Step 7 BoM Spreadsheet Link](https://docs.google.com/spreadsheets/d/e/2PACX-1vTVx7BvB3V7CozF2l4eWkNntWrHSjOawmrsi_bRSVxQLIGVlfZTYEGp8a6fHpENV6hV2cn9PrDLHHl0/pubhtml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)

### Prep
1. Clean support material out of any nut traps and holes.

    \
    *fig 7.1*

### Assembly
1. Prepare the x carrage top by inserting an M3 nut in the nut trap on the underside.

    \
    *fig 7.2*

1. Attach the X carriage top to the X linear rail with the 4 M3 x 10mm screws. *The top carriage isn't perfectly symmetrical so make sure that it is flush or overhangs the sides of the linear rail carriage*

    \
    *fig 7.3*

2. Prepare the front plate by inserting 2 of the M3 40mm screws and 4 of the M3 nuts into the nut traps. If the nuts are loose, use blue tape temporarily secure them.

    \
    *fig 7.4*

    \
    *fig 7.5*

3. Now carefully attach the front plate to the top plate by inserting the M3 40mm screws through the top plate thru holes.

    \
    *fig 7.6*

4. Prepare the back plate by inserting an M3 nut into the nut trap. *If it's loose secure it with blue tape*

    \
    *fig 7.7*

    \
    *fig 7.8*

5. Attach the back plate to the top plate.

    \
    *fig 7.9*

6. Hand tighten 2 M3 nuts onto the ends of the M3 40mm screws. Then carefully remove the blue tape you used to hold the nuts in place. They should now be held captive by the linear carriage and top carriage.

    \
    *fig 7.10*

    \
    *fig 7.11*

7. Finish tightening the nuts using the hex wrech and M3 screw driver.

    \
    *fig 7.12*

8. Using the remaining 2 M3 x 40mm screws secure the bottom plate by sandwitching it between the front and back plates. *You'll be removing the bottom plate in a later step do don't worry about attaching switches or the correct orientation.*

    \
    *fig 7.13*

    \
    *fig 7.14*

9. Here is what you should have when you are done. We just need enough to secure the belts. We'll do the rest later

    \
    *fig 7.15*

    \
    *fig 7.16*

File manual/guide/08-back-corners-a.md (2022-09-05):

# My BLV MGN Cube - Step 8 Partially Build Back Corners

## [Step 8 BoM Spreadsheet Link](https://docs.google.com/spreadsheets/d/e/2PACX-1vTVx7BvB3V7CozF2l4eWkNntWrHSjOawmrsi_bRSVxQLIGVlfZTYEGp8a6fHpENV6hV2cn9PrDLHHl0/pubhtml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)

### Prep
1. Install 4x M5 10mm screws and T-nuts in the left corner block.

    \
    *fig 8.1*

2. Install 3x M5 10mm screws and T-nuts in the right corner block and 1x M5 10mm screw and T-nut in the right aux block.

    \
    *fig 8.2*

### Assembly
1. Attach left block to the upper left inside corner of the frame.

    \
    *fig 8.3*

2. Insert 3x M3 35mm screws in to the lower left block. Use some blue tape to keep them from falling out.

    \
    *fig 8.4*

3. Attach right block to the upper right inside corner of the frame.

    \
    *fig 8.5*

4. Position the Right aux block so it lines up with the 2 holes on the front edge of the right block.

    \
    *fig 8.6*

5. Insert 3x M3 35mm screws through the right aux block. 2 will also go through the right block. Use blue tape to keep them from falling out.

    \
    *fig 8.7*

6. Tighten the M5 10mm and T-nut on the bottom of the right aux block.

    \
    *fig 8.8*

7. Assemble a idler stack on each M3 35mm screw. As before you'll be making a sandwich of washers and bearings. *(washer->bottom flanged bearing->washer->top flanged bearing->washer)*

    \
    *fig 8.7*

    \
    *fig 8.8*

    \
    *fig 8.9*

8. Temporarily use M3 nuts to hold the idlers on the M3 25mm screws and remove the blue tape. *We're doing this so we can run the belts before things get covered up*

    \
    *fig 8.10*

    \
    *fig 8.11*

    \
    *fig 8.12*

9. Calculate the position of the Left pulley on the stepper. I wound up at 6.95mm from the stepper to the bottom of the pulley.

    \
    *fig 8.13*

    \
    *fig 8.14*

    \
    *fig 8.15*

10. Set the Left pulley on the Stepper according to the measurement and carefully tighten. Don't overtighten!! Stripping set screws is no fun.

    \
    *fig 8.16*

11. Attach the left stepper to the bottom block using 1x M3 8mm (permanent) and 2x M3 35mm with M3 nuts as spacers (temporary).

    \
    *fig 8.17*

12. Calculate the position of the Right pulley on the stepper. I wound up at 7.27mm from the stepper to the bottom of the pulley.

    \
    *fig 8.18*

13. Set the Right pulley on the Stepper according to the measurement and carefully tighten. Don't overtighten!! Stripping set screws is no fun.

    \
    *fig 8.19*

    \
    *fig 8.20*

14. Attach the right stepper to the bottom block using 1x M3 8mm (permanent) and 3x M3 35mm with M3 nuts as spacers (temporary).

    \
    *fig 8.21*

    \
    *fig 8.22*

15. Here's what it should look like when this step is done.

    \
    *fig 8.23*

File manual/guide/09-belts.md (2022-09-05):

# My BLV MGN Cube - Step 9 Install Belts

## [Step 9 BoM Spreadsheet Link](https://docs.google.com/spreadsheets/d/e/2PACX-1vTVx7BvB3V7CozF2l4eWkNntWrHSjOawmrsi_bRSVxQLIGVlfZTYEGp8a6fHpENV6hV2cn9PrDLHHl0/pubhtml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)

### Assembly
1. Thread the end of the belt through the front left opening on the X-carriage. A zip tie can be handy to guide the belt through the hole. Stick the zip tie into the hole far enough that it bends and goes parallel to the extrusion. Then thread the belt along the zip tie and out the hole.

    \
    *fig 9.1*

2. Secure the end of the belt with 2 zip ties. Ideally the teeth of the belt would be folded together but I did the reverse to keep the belt as close to the extrusion as possible. Pay attention to the zip tie orientation to prevent the end of the zip tie from rubbing.

    \
    *fig 9.2*

3. Thread the belt through the front idler on the Left X mount.

    \
    *fig 9.3*

4. Remove the idler holder from the Left tensioner block and thread the belt through the idler holder.

    \
    *fig 9.4*

5. Reattach the idler holder to the tensioner block using the tensioner knob. Once the nut grabs M4 bolt give it 6-7 full turns to provide the tensioner some headroom if you need to loosen it after attaching the belts. *If the nut is loose you can use the big end of a zip tie to hold it in place*

    \
    *fig 9.5*

6. Now run the belt past the Left X mount in the gap between the extrusion.

    \
    *fig 9.6*

7. Thread the belt through the Left corner block and over the stepper pulley.

    \
    *fig 9.7*

8. Now flip the belt and run through the lower idler on the Right block. *the flat part of the belt should be against the right idler*

    \
    *fig 9.8*

    \
    *fig 9.9*

9. Thread the belt through the back idler on the Right X mount. *you can use a zip tie as a guide*

    \
    *fig 9.10*

10. Thread the end of the belt through the back right opening on the X-carriage. A zip tie can be handy to guide the belt through the hole. Stick the zip tie into the hole far enough that it bends and goes parallel to the extrusion. Then thread the belt along the zip tie and out the hole.

    \
    *fig 9.11*

11. Using a pen wedged between the X carriage and the front Left X mount idler pull on the belt end to take up the slack. **Don't pull hard/tighten the belt.** You need both belts in place otherwise you'll rack the X rail and in any case the back corner pulleys are only partially secured. We'll use the tensioners later in the build to properly tension the belts.

    \
    *fig 9.12*

12. Secure the belt end, teeth facing out, with 2 zip ties. Teeth facing out isn't ideal but it's better to have the belt more in line than have a tooth to tooth connection. Also pay attention the the zip tie orientation/spacing so they won't get in the way during operation. Also now is the time to trim the belt. You'll use the remainder for the next run. I personally left 50mm, from the edge of the x carrage and had plenty for the 2nd belt run.

    \
    *fig 9.13*

13. Here is what it should look like at this point with the lower belt attached.

    \
    *fig 9.14*

14. Thread the end of the belt through the front right opening on the X-carriage. A zip tie can be handy to guide the belt through the hole. Stick the zip tie into the hole far enough that it bends and goes parallel to the extrusion. Then thread the belt along the zip tie and out the hole.

    \
    *fig 9.15*

15. Secure the end of the belt with 2 zip ties. Ideally the teeth of the belt would be folded together but I did the reverse to keep the belt as close to the extrusion as possible. Pay attention to the zip tie orientation to prevent the end of the zip tie from rubbing.

    \
    *fig 9.16*

16. Thread the belt through the front idler on the Right X mount.

    \
    *fig 9.17*

17. Remove the idler holder from the Reft tensioner block and thread the belt through the idler holder.

    \
    *fig 9.18*

18. Reattach the idler holder to the tensioner block using the tensioner knob. Once the nut grabs M4 bolt give it 6-7 full turns to provide the tensioner some headroom if you need to loosen it after attaching the belts. *If the nut is loose you can use the big end of a zip tie to hold it in place*

    \
    *fig 9.19*

19. Now run the belt past the Right X mount in the gap between the extrusion.

    \
    *fig 9.20*

20. Thread the belt through the Right corner block and over the stepper pulley.

    \
    *fig 9.21*

21. Now flip the belt and run through the upper idler on the Left block. *the flat part of the belt should be against the right idler*

    \
    *fig 9.22*

    \
    *fig 9.23*

22. Thread the belt through the back idler on the Left Mount. *you can use a zip tie as a guide*

    \
    *fig 9.24*

23. Thread the end of the belt through the back left opening on the X-carriage. A zip tie can be handy to guide the belt through the hole. Stick the zip tie into the hole far enough that it bends and goes parallel to the extrusion. Then thread the belt along the zip tie and out the hole.

    \
    *fig 9.25*

24. Pull on the belt end to take up the slack and secure with 2 zip ties. **Don't pull hard/tighten the belt.** You need both belts in place otherwise you'll rack the X rail and in any case the back corner pulleys are only partially secured. We'll use the tensioners later in the build to properly tension the belts.

    \
    *fig 9.26*

25. Here is what it should look like with all the belts attached.

    \
    *fig 9.27*

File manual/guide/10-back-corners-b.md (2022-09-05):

# My BLV MGN Cube - Step 10 Finish Building Back Corners

## [Step 10 BoM Spreadsheet Link](https://docs.google.com/spreadsheets/d/e/2PACX-1vTVx7BvB3V7CozF2l4eWkNntWrHSjOawmrsi_bRSVxQLIGVlfZTYEGp8a6fHpENV6hV2cn9PrDLHHl0/pubhtml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)

### Prep
1. Install 3x M5 10mm screws and T-nuts on the left and right corner tops.

    \
    *fig 10.1*

### Assembly
1. On the Left block, remove the 2x M3 35mm Socket Head Cap Screws and idler nuts temorarily installed in step 8. Make sure to use tape to keep the M3 bolts holding the idlers from falling out the bottom of the block.

    \
    *fig 10.2*

    \
    *fig 10.3*

    \
    *fig 10.4*

2. Place the Left corner top and reattach the stepper motor using 3x M3 35mm Socket Head Cap Screws. Don't tighten the M5 Bolts yet.

    \
    *fig 10.5*

3. Secure the idler M3 bolts using 3x M3 locknuts.

    \
    *fig 10.6*

4. Now tighten down the M5 bolts to finish securing the left corner top.

    \
    *fig 10.7*

5. Install the left corner cap.

    \
    *fig 10.8*

5. Repeat for the right side but use the M3 25mm Socket Head Cap Screws, temporarily installed in Step 8, to secure the stepper. Here's what it should look like when you're done.

    \
    *fig 10.9*

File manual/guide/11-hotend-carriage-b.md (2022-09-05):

# My BLV MGN Cube - Step 11 Finish Building Hotend Carriage

## [Step 11 BoM Spreadsheet Link](https://docs.google.com/spreadsheets/d/e/2PACX-1vTVx7BvB3V7CozF2l4eWkNntWrHSjOawmrsi_bRSVxQLIGVlfZTYEGp8a6fHpENV6hV2cn9PrDLHHl0/pubhtml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)

### Prep

1. Solder 15cm lengths of black and green wires onto the limit switch. The black wire should attach to the Common (COM) terminal and the green wire should attach to the Normally Closed (NC) terminal. *It's important to use NC instead of NO. If a wire breaks it will automatically trigger the endstop*

    \
    *fig 11.1*

2. Test the limit switch and wiring using the continuity tester on your Multimeter. It should be a closed circuit until you press the switch.

    \
    *fig 11.2*

3. Make sure the heater cartridge and thermistor wires come out this side of the heater block.

    \
    *fig 11.3*

### Assembly
1. Remove the 2 lower M3 40mm Socket Head Cap Screws/Nuts from the X carrage and remove the bottom of the carriage. *Belts should be a little loose so it doesn't stress the rest of the carriage*

    \
    *fig 11.4*

2. Dip the ends of the 2 M2 15mm Philips Pan Head Screws in threadlocker.

    \
    *fig 11.5*

3. Insert the 2 M2 15mm screws in to the lower X carrage as shown. You'll notice that I snapped off the bridge on this piece and I'm using M2's instead of M2.5s. This works much better, in reality, than what's described in BLV's hotend assembly video.

    \
    *fig 11.6*

4. Attach the limit switch to the lower X carrage using the M2 screws and nuts. You may need to file down the sides of the carraige to get the switch to fit. Don't overtighted the screws as the switch is delicate and you can crush the hollow casing. Note how I routed the wires.

    \
    *fig 11.7*

5.  Insert an M3 nuts into the fan blower as shown. *Don't worry about the other hole*

    \
    *fig 11.8*

6. Using the M3 14mm Socket Head Cap Screw, attach the fan blower to the lower X carriage.

    \
    *fig 11.9*

7. Put 10mm of heat shrink tubing over both wires and then solder the wires as shown. Then slide the tubing over the exposed terminals of the male JST connector and apply heat to the shrink the tubing with the Mini Butane Torch. **NOTE: Take a look at the soldering procedure in [Build Bowden Extruder and Hotend Wiring Harness](16-extruder-hotend-harness.md) it's much better**

    \
    *fig 11.10*

    \
    *fig 11.11*

    \
    *fig 11.12*

8. Reattach the lower X carriage to the rest of the X carriage using the M3 40mm screws/nuts. *I used some threadlocker on the nuts for good measure*

    \
    *fig 11.13*

9. Zip tie the limit switch wiring to the back X carriage.

    \
    *fig 11.14*

10. Cleanup and trim the belts. Now is a good time to trim your belts and verify the limit switch can trigger without the belts catching in the idlers. *I also had to redo some of my zip ties so I could trim the belts closer*

    \
    *fig 11.15*

11. Insert the 2 M3 25mm Socket Head Cap Screws, with washers, into the 5015 blower fan.

    \
    *fig 11.16*

12. Put the Fan mount over the screw ends.

    \
    *fig 11.17*

13. Secure the screw closest to the blower opening with a lock nut. *Don't overtighten or you will damage the fan*

    \
    *fig 11.18*

14. Attach the blower fan to the X carraige and blower duct. Make sure the mouth of the blower is inserted into the duct correctly. *Don't overtighten or you will damage the fan*

    \
    *fig 11.19*

15. Secure the blower fan wores and limit switch wires with a zip tie to the mount point on the back x carrage plate. Leave a little slack on the blower wire but make sure it doesn't run into the linear rail mount when the carriage is all the way to the left. *You should have a little more slack for the limit switch connecter than what you see in this pic. I updated the directions after realizing it was too short*

    \
    *fig 11.20*

16. Attach the Hotend to the X Carrage.

    \
    *fig 11.21*

17. Attach the PTFE tubing to the hotend and then secure the hotend using the BLTouch Locker and 2 M3 30mm Socket Head Cap Screws. *To insert the tubing into the hotend, remove the orange clip and press down on the fitting then reattach the clip to secure it.*

    \
    *fig 11.22*

18. Connect the cable locker using the M3 14mm Socket Head Cap Screw. Make sure it grabs the nut embedded in the X carriage. If the screw bottoms out before it's tight use some M3 washers. The orientation of the cable locker is important. The bumps/lower offset should point towards the front.

    \
    *fig 11.23*

19. Using the 2 M3 10mm Socket Head Cap Screws and nuts and washers. Secure the BLTouch to the locker mount. Make sure the BLTouch probe is secure but don't overtighten or you might damage it.

    \
    *fig 11.24*

20. Route the BLTouch and 4010 fan wires through the bottom opening in the cable locker.

    \
    *fig 11.25*

21. Using the 4x M3 18mm Socket Head Cap Screws attach the Block Sheild to the front of the X carriage. Make sure the 4010 fan is oriented so it will blow air across the heat sink. Also route the BLTouch probe wires inside the Block Sheild making sure not to pinch them.

    \
    *fig 11.26*

    \
    *fig 11.27*

    \
    *fig 11.28*

    \
    *fig 11.29*

    \
    *fig 11.30*

21. Now route and zip tie the heater cartridge and thermistor wires so they are out of the way.

    \
    *fig 11.31*

22. Here's what it should look like when everything is done.

    \
    *fig 11.32*

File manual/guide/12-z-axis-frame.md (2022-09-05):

# My BLV MGN Cube - Step 12 Z Axis Frame

## [Step 12 BoM Spreadsheet Link](https://docs.google.com/spreadsheets/d/e/2PACX-1vTVx7BvB3V7CozF2l4eWkNntWrHSjOawmrsi_bRSVxQLIGVlfZTYEGp8a6fHpENV6hV2cn9PrDLHHl0/pubhtml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)

### Prep
1. Print 1 main jig in PLA
    1. Measure the 60mm section with the Digital Calipers.

        \
        *fig 12.1*

    2. Calculate the scale factor using this equation:

        Scale Factor=(60mm/Measured Value) * 100

    3. Print 2 Main Jigs in PLA with using the scale factor

2. File down the ridge of the Z Stopper. It's too high and will interfere when attaching the T-Nut to the extrusion.

    \
    *fig 12.2*

3. Loosely attach the Z Rail Stoppers to the 496mm extrusions. The allen key will have just enough space to tighten when the extrusion in in the frame.

    \
    *fig 12.3*

### Assembly
1. Temporarily install a pair of Angle Brackets on the front and back uprights of the left side frame. These will help to position the 442mm extrusion later.

    \
    *fig 12.4*

    \
    *fig 12.5*

2. Carefully slide the 496mm extrusion below the 90 degree joining plates on the Left side of the frame. Make sure the Z stopper is in the correct channel and facing the right way.

    \
    *fig 12.6*

3. Temporarily use the 2 442mm extrusions to correctly position the upper 496mm extrusion. Lightly secure with the clamps. Don't use too much pressure on the clamps or you might bend the extrusions.

    \
    *fig 12.7*

4. Temporarily attach 3 Flat Corner Braces, using M5 8mm Screws and T-nuts, to the 496mm extrusion and uprights to secure it. 2 braces on the outside and 1 brace on the front inside. Make sure that there isn't a gap between the 496mm extrusion and the tops of the 442mm extrusions.

    \
    *fig 12.8*

5. Remove the clamps and 2 442mm extrusions. Add addtional M5 8mm Screws and T-nuts to the Angle Brackets you attached in Step 1 and readjust them to permaently attach the 496mm extrusion.

    \
    *fig 12.9*

    \
    *fig 12.10*

6. Remove the 3 Flat Corner Braces.

    \
    *fig 12.11*

7. Repeat Steps 1-6 to properly attach the 496mm extrusion on the right side. It should look like this when you are done.

    \
    *fig 12.12*

8. Carefully insert a 442mm extrusion and attach 4 Flat Corner Braces, but only to the vertical 442mm extrusion and not the horizontal extrusions. We're using the braces to keep the extrusion flush and square but you need to be able to slide it in the next step.

    \
    *fig 12.13*

9. Using the 2 Main Jigs, set the distance between the 442mm extrusion and the front of the printer frame. The jigs are used on alternate sides of the extrusion to keep the 442mm extrusion as square as possible. I used some tape to keep the jigs in place.

    \
    *fig 12.14*

10. Tighten the M5 screws on all flat corner braces, horizontal sections, attaching the 442mm Extrusion to the top and bottom extrusions. Only the bottom braces are shown but you should do the top ones as well.

    \
    *fig 12.15*

11. Use 8 Angle Brackets to attach the top and bottom of the 442mm extrusions to the frame. Losely tighten the brackets (extrusion side first) as the example picture shows. After everything is aligned, do the final tightening in the same order.

    \
    *fig 12.16*

    \
    *fig 12.17*

    \
    *fig 12.18*

12. Now remove the Flat Corner Braces and the left side is done.

    \
    *fig 12.19*

14. Position and tighten the Left Z Rail Stopper above the 442mm Extrusion.

    \
    *fig 12.20*

13. Repeat Steps 8-14 for the right side. This is what it should look like when you are finished.

    \
    *fig 12.21*

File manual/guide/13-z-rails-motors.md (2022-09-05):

# My BLV MGN Cube - Step 13 Z Rails and Motors

## [Step 13 BoM Spreadsheet Link](https://docs.google.com/spreadsheets/d/e/2PACX-1vTVx7BvB3V7CozF2l4eWkNntWrHSjOawmrsi_bRSVxQLIGVlfZTYEGp8a6fHpENV6hV2cn9PrDLHHl0/pubhtml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)

### Prep
1. Attach 8x M3 8mm socket head cap screws and T-Nuts into every other hole of the 2 linear rails. Leave a open hole at the top of each rail.

    \
    *fig 13.1*

2. File down the Z rail stoppers and Z motor mounts so that the T-Nuts will have enough space to grab the extrusion.

    \
    *fig 13.2*

    \
    *fig 13.3*

    \
    *fig 13.4*

### Assembly

1. Attach the left linear rail to the 442mm Z extrusion. Use the 2x 2020 jigs to center the rail on the extrusion and tighten in the pattern indicated. Make sure there isn't a gap between the linear rail and the top Z rail stopper.

    \
    *fig 13.5*

    \
    *fig 13.6*

2. Attach the lower Z rail stopper using an M5 10mm screw and T-Nut.

    \
    *fig 13.7*

3. With the top and bottom stoppers in place you can now remove any shipping stoppers on the rail.

    \
    *fig 13.8*

4. Attach Left Mgn Mount to the MGN Carriage using 4x M3 8mm screws.

    \
    *fig 13.9*

5. Attach the Left motor mount at the intersection of the 442mm Z Extrusion and the 496mm left side horizontal extrusion.

    \
    *fig 13.10*

6. Attach the left Z stepper motor to the motor mount using 4x M3 12mm screws and washers.

    \
    *fig 13.11*

7. Repeat assembly steps for the right side. This is what you should have when you are done.

    \
    *fig 13.12*

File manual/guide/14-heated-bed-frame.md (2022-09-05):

# My BLV MGN Cube - Step 14 Build Heated Bed Frame and Finish Z-Axis

## [Step 14 BoM Spreadsheet Link](https://docs.google.com/spreadsheets/d/e/2PACX-1vTVx7BvB3V7CozF2l4eWkNntWrHSjOawmrsi_bRSVxQLIGVlfZTYEGp8a6fHpENV6hV2cn9PrDLHHl0/pubhtml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)

### Prep
1. File down the 4x bed holders so that the T-Nuts will have enough space to grab the extrusion.

    \
    *fig 14.1*

2. Find a the flattest surface in your house. Hint, If you have a granite counter top that's probably the best. Make sure it's clean and then use one of your pieces of extrusion as a straight edge and a piece of paper as a thickness guage. Try and slip a piece of paper under the extrusion in a couple of places to test for flatness. Test multiple directions. Probably won't be perfect but pick the best counter you have. This will be the surface you use to build the frame.

    \
    *fig 14.2*

3. Cover the surface in a large piece of craft paper to protect it. *Can't build a 3d printer if your significant other murders you for scratching their counter top with sharp edged extrusions*

### Assembly

1. Attach 2 corner braces to each of the 173mm extrusions so they overlap the ends by about 10mm but less than 20mm. You'll use these as a guide to keep them flush with the ends of the 405mm extrusions in the next step.

    \
    *fig 14.3*

2. Clamp the 2x 405mm extrusions to one of the 173mm extrusions using the corner braces in the last step. Make sure the 172mm extrusion is flush with the ends of the 2x 405mm extrusions.

    \
    *fig 14.4*

3. Using 2 of the angle brackets, with M5 8mm screws and T-nuts, permanently attach the 173mm extrusion to the 2x 405mm extrusions. Start by loosely tightening (#1 then #2) then finish tightening sequence (#3 then #4). The sequence is important to get the bracket aligned and make sure the 173mm extrusion is flush with the ends of the 405mm extrusions.

    \
    *fig 14.5*

4. Clamp the 173mm extrusion on the other other side. Make sure it is flush with with the ends of the 405mm extrusions.

    \
    *fig 14.6*

5. Repeat what you did in step 3. Using 2 of the angle brackets, with M5 8mm screws and T-nuts, permanently attach the 173mm extrusion to the 2x 405mm extrusions. Start by loosely tightening (#1 then #2) then finish tightening sequence (#3 then #4). The sequence is important to get the bracket aligned and make sure the 173mm extrusion is flush with the ends of the 405mm extrusions.

    \
    *fig 14.7*

6. Remove the angle brackets and clamps so you can install the 4x frame covers using M5 10mm screws and T-Nuts. I fastened the covers on the 173mm extrusions (see arrows). *Note: my frame wasn't completely flat but that's fine because the bed is adjustable and mounting it to the 3D printer will probably help with this*

    \
    *fig 14.8*

7. Now install the bed holders onto the 405mm extrusions. You will need to put the top T-Nut into the extrusion, first, and then snap the bed holder in place. Once it is in place, loosely tighten the screws but make sure that the bed holders can still slide along the extrusions.

    \
    *fig 14.9*

    \
    *fig 14.10*

8. Here is what the bed frame should look like with all 4 of the bed mounts attached.

    \
    *fig 14.11*

9. Temporarily attach the heated bed to the 4 bed holders on the bed frame. Use the M4 35mm flat head screws, washers, bed leveling springs, and some M4 nuts. We'll use the bed to correctly position the 4 bed holders in the next step.
   **Note: The bed pictured is different from the one I eventually used and specified in the BoM.** 

   \
   *fig 14.12*

   \
   *fig 14.13*

10. Slide the loose bed holders so that the heated bed is centered on the bed frame.

   \
   *fig 14.14*

11. Now tighten the 2x M5 screws on the sides of each bed holder to fix them in place on the bed frame.

    \
    *fig 14.15*

12. Remove the heated bed so you can tighten the M5 screw on the top of each bed holder. So it doesn't get in the way we'll leave the bed off and reattach the bed in a later step.

    \
    *fig 14.16*

13. Turn the bed holder over and loosely attach the Z mount left and right blocks using the M5 10mm screws and T-nuts. Just the bottom facing screws and T-nuts. We'll insert the 2 side screws and T-nuts later.

    \
    *fig 14.17*

14. Using the calipers score the center point of the 173mm extrusion and use it to center the blocks. Now you can tighten down the M5 screw on each block

    \
    *fig 14.18*

    \
    *fig 14.19*

15. Use 4x M3 35mm screws and lock nuts to attach the lead screw nuts to each Z mount block. Use the 5.5mm wrench to hold the lock nuts.

    \
    *fig 14.20*

    \
    *fig 14.21*

16. With the printer on it's side (Left side facing up) add 2 T-Nuts to the left side of the bed frame. Make sure to put something on the floor to protect the printer and the floor (I have foam tiles on my floor).

    \
    *fig 14.22*

17. Use a zip tie to help position the T-nuts under the holes while you fasten the left Z mount block to the left MGN mount.

    \
    *fig 14.23*

    \
    *fig 14.24*

18. Now carefully put the printer on it's other side and attach the right Z mount block to the right MGN mount in the same way. This was tricky. Make sure not to let the bed crash or twist. Test the bed frame by sliding on the rails and adjust the Z mount block as necessary if it binds.

    \
    *fig 14.25*

    \
    *fig 14.26*

19. Install the lead screws in the left and right Z mount blocks by threading into the lead screw nuts.

    \
    *fig 14.27*

20. Attach the lead screws to the Z steppers using 2x flexible couplers. Make sure to tighten enough so that the stepper and lead screws don't slip but careful not to strip the set screws.

    \
    *fig 14.28*

21. When you are done here's what the final product should look like.

    \
    *fig 14.29*

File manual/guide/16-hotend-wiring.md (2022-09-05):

# My BLV MGN Cube - Step 16 Hotend Wiring

## [Step 16 BoM Spreadsheet Link](https://docs.google.com/spreadsheets/d/e/2PACX-1vTVx7BvB3V7CozF2l4eWkNntWrHSjOawmrsi_bRSVxQLIGVlfZTYEGp8a6fHpENV6hV2cn9PrDLHHl0/pubhtml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)

### Assembly
1. Check your fan connectors for the correct polarity. -/Black and +/Red should be in the JST-XH connector as pictured. My blower fan was wired backwards. It's easy to remove the female pins and swap them in the connector if you need to. Aliexpress cheap but...

    \
    *fig 16.1*

2. Make extension wires for the both fans using 1m lengths of the 22AWG silicone wire and 2pin male connectors.
    1. Cut pieces of heat shrink tubing for each wire and slide over the wires. Use a larger piece of heat shrink tubing to cover all the wires. *Nothing is more annoying than realizing you forgot to put the heat shrink tubing on a wire after you're done attaching the connectors*

        \
        *fig 16.2*

    2. Strip the ends of the wires. Only strip a little because we are going to crimp the ends with female JST-XH connectors.

        \
        *fig 16.3*

    3. Attach female JST-XH crimps to the ends of the wires using the crimper. *The IWS-2820M worked much better than the fancy ratcheting ones for me. It's not fast but I got much better crimps.*

        \
        *fig 16.4*

    4. Setup the male connector in your helping hands and use the female crimps to attach to the back the connector. This will make soldering them MUCH easier. Also make sure to attach something to the connector to help dissipate the heat when you solder it (I used a spare fan). The connectors are really small and you're likely to melt it if you don't dissipate the heat somehow.

        \
        *fig 16.5*

    5. Solder the female connectors to make it permanent. You shouldn't need much. Be quick to avoid melting the connector.

        \
        *fig 16.6*

    6. Slide the heat shrink tubing over each connection and use the torch to shrink it. I wave the torch back and fourth to keep the heat even and to avoid melting/burning things.

        \
        *fig 16.7*

        \
        *fig 16.8*

3. Make an extension wire for the limit switch using 1m lengths of the 22AWG silicone wire and a 3pin female connector. Preferably green for signal and black for common.

    \
    *fig 16.9*

4. Test the fans for proper operation.
    1. Temporarily wire up the power supply. **CAUTION: You're messing with mains power here and it can kill you. Use your own common sense here and consult a professional if you are unsure on how to do this**

        \
        *fig 16.10*

    2. Select the correct mains voltage on the power supply (Red Switch on Side)

        \
        *fig 16.11*

    3. Connect up the fans and power on the supply to check that they are working correctly. The hotend cooling fan should be sucking in air through the front grill and the part cooling fan should be blowing air around the nozzle.

        \
        *fig 16.12*

5. Test hotend compents and wires.
    1. Test the X-axis limit switch using the multimeter contunity tester. The switch should be wired as normally closed. If the switch wiring breaks or is disconnected it will automatically trigger the switch. Here you see the switch is depressed and my multimeter has registered the circuit as open.

        \
        *fig 16.13*

    2. Test the hotend heater cartridge using the multimeter set to read resistance. You're really just looking for a finite resistance, probably 12-13 Ohms. If you are interested in the math V*V/R=W so in my case 24V*24V/12.8Ohms=45W.

        \
        *fig 16.14*

    3. Test the hotend thermistor. Standard thermistors, like mine, are in the 100K Ohm range. This math is non-trivial so be happy with something finite.

        \
        *fig 16.15*

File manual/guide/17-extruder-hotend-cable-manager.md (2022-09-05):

# My BLV MGN Cube - Step 17 Build Bowden Extruder and Hotend Cable Manager

Note: The cable management system here is something I created. It diverges from the standard build which didn't do much for cable management. If you find an issue please let me know by creating an issue in the GitHub project.

## [Step 17 BoM Spreadsheet Link](https://docs.google.com/spreadsheets/d/e/2PACX-1vTVx7BvB3V7CozF2l4eWkNntWrHSjOawmrsi_bRSVxQLIGVlfZTYEGp8a6fHpENV6hV2cn9PrDLHHl0/pubhtml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)

### Prep
1. Remove any sharp edges on the inside of the flex tube reinforcers.

    \
    *fig 17.1*

### Assembly
1. Place the M3 Square nut in the frame cable locker and use an M3 8mm screw to secure itkl.

    \
    *fig 17.2*

2. Attach the frame cable locker with 2x M5 8mm screws and T-nuts centered on the top back extrusion.

    \
    *fig 17.3*

3. Place the mounting plate on the stepper motor and measure a 2mm gap from the plate to the botton of the BMG extruder gear. Carefully tighten the set screw. **DON'T OVERTIGHTEN THE SET SCREW OR IT WILL STRIP**

    \
    *fig 17.4*

4. Separate the BMG extruder and insert the bowden adapter.

    \
    *fig 17.5*

5. Make a BMG/Extruder Mount/Stepper sandwich. To help the stepper/gear insert into the BMG extruder try gently wobbling it. Note stepper wires are on the left.

    \
    *fig 17.6*

6. Complete the extruder mount using 3x M3 35mm screws.

    \
    *fig 17.7*

7. Using 2x M5 10mm and T-nuts attach the extruder to frame with the bowden hole on the printer centerline.

    \
    *fig 17.8*

    \
    *fig 17.9*

7. Attach the BMG extruder tensioner.

    \
    *fig 17.10*

8. Insert 10 of the flex tube reinforcers into the 62cm flex tube as indicated by the pictre. The reinforcers are spaced about 9cm apart (center to center). There are 2 reinforcers at one end, for the hotend locker, and 3 reinforcers at the other end, for the frame locker.

    \
    *fig 17.11*

9. Carefully insert the cables into the flex tube and through the reinforcers. Try not to twist the cables around one another in the tube. Don't put connectors inside of the tube.

    \
    *fig 17.12*

10. Using 3x small zip ties secure the end of the flex tube, that has 2 reinforcers, to the Hotend cable locker. The flex tube slit should be centered on the locker. Secure any loose wires using zip ties (Ugly, but it works for now). Again: Connecters inside the flex tube is bad.

    \
    *fig 17.13*

    \
    *fig 17.14*

11. Thread the large zip tie into the hotend locker until the head of the zip tie clicks into place.

    \
    *fig 17.15*

12. Thread the PTFE tube and large zip tie onto the hotend cable guides and use the small zip ties to secure to the flex tube. The cable guide has a notch that should align with the reinforcer lips. The slit on the flex tube should be on top.

    \
    *fig 17.16*

    \
    *fig 17.17*

    \
    *fig 17.18*

13. Insert the large zip tie end and flex tube into the frame locker. Also cut the PTFE tube and insert into the extruder. Tighten the M3 to clamp the end of the zip tie. Around 79cm is what my PTFE tube mesured.

    \
    *fig 17.19*

14. Secure the frame locker using 3 small zip ties. *Note: I didn't use the top hole to allow the flex tube a little more play.*

    \
    *fig 17.20*

14. Here is how the final cable guide should look.

    \
    *fig 17.21*

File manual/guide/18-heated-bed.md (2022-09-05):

# My BLV MGN Cube - Step 18 Install Heated Bed

The heated bed is one of the most likely components on a 3d printer to catch fire. I'm accepting the risk for myself on what I'm doing here. If you aren't comfortable doing the same then please consult a professional. If you think I'm doing something unsafe and stupid please let me know by raising an issue for the GitHub project.

## [Step 18 BoM Spreadsheet Link](https://docs.google.com/spreadsheets/d/e/2PACX-1vTVx7BvB3V7CozF2l4eWkNntWrHSjOawmrsi_bRSVxQLIGVlfZTYEGp8a6fHpENV6hV2cn9PrDLHHl0/pubhtml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)

### Prep
1. Test the heat bed to determine it's wattage and make sure it doesn't have a short. Using the multimeter set to read resistance, measure the restisance between the red and black wires. Use the formula Volts * (Volts/Resistance) = Watts to determine the Wattage. In my case, 24V * (24V/2.5 Ohms) = 230 Watts.

    \
    *fig 18.1*

    Note: Big Tree Tech recommends an external mosfet for anything over 144 Watts so I'll definitely be using a $10 external Mosfet to keep my board from catching on fire. Also it will probably increase the life for other controller boards as they'll run a lot cooler.

2. Test the thermistor to make sure it isn't shorted or there isn't a loose wire. Using the multimeter set to read resistance, measure the restisance between the yellow thermistor wires. I get around 111 KOhms at room temperature which is good. As long as you get a reading in KOhms you're probably good.

    \
    *fig 18.2*

3. Attach the heated bed insulation.
    1. Measure and cut holes for bed leveling springs.

        \
        *fig 18.3*

        \
        *fig 18.4*

    2. Clean the bottom of the heated bed with alcohol and then apply the insulation.

        \
        *fig 18.5*

        \
        *fig 18.6*

    3. Make sure to trim the metal backing away from any power connectors.

        \
        *fig 18.7*

4. Attach the magnetic sheet to the heated bed.
    1. Create a ledge to help align the magnetic sheet. *I used some scrap wood*

        \
        *fig 18.8*

    2. Test fit the magnetic sheet on the build plate.

        \
        *fig 18.9*

    3. Remove the protective film on the heated bed.

        \
        *fig 18.10*

    4. Clean the build plate with alcohol and make sure it is free of dust/dirt/cat hair etc..

        \
        *fig 18.11*

        Note: I had a little blemish on my aluminum plate that I sanded down with 1000 grit wet sandpaper.

    5. Peel back ~4cm of the paper backing on one edge of the magnteic bed and carefully apply to heated bed using the ledge as a guide.

        \
        *fig 18.12*

    6. Using a platic spreader (or an old plastic credit card) smooth down the exposed part of the magnetic sheet to prevent air bubbles from getting trapped underneath.

        \
        *fig 18.13*

    7. Keep peeling back paper, 4cm at a time, and smoothing down with the spreader until the entire magnetic sheet is attached to the heated bed. If you go slow and are careful you shouldn't have any air bubbles trapped under the sheet. 

        \
        *fig 18.14*

        \
        *fig 18.15*

    8. Once fully attached flip over and use an X-acto knife to trim the excess material.

        \
        *fig 18.16*

    9. Using the heated bed mounting holes as a guide, poke through the underside of the magnetic sheet using the X-acto knife. This will help you find the mounting holes from the top.

        \
        *fig 18.17*

        \
        *fig 18.18*

    5. Use some blue tape to protect the surface around the mounting hole.

        \
        *fig 18.19*

    6. Using the X-Acto knife, cut out the hole. I found doing this slowly with small shavings worked best.

        \
        *fig 18.20*

        \
        *fig 18.21*

        \
        *fig 18.22*

5. Insert M4 nuts in each bed leveling knob. Regular nuts are fine because the tension with the bed leveling springs will keep everything tight.

    \
    *fig 18.23*

6. Put M3 square nuts and M3 10mm screws into each wireguide mount. Also attach 2x M5 8mm and T-Nuts.

    \
    *fig 18.24*

7. Cut the ratchet end off the 24" zip tie.

    \
    *fig 18.25*

### Assembly
1. Attach the heatbed wireguide bedmount (Long one) to the bed frame placing it ~120mm from the bed frame corner to the edge of the mount.

    \
    *fig 18.26*

2. Attach the heatbed wireguide framemount to the top back 2020 extrusion so that it's centered on the frame (~248mm for me).

    \
    *fig 18.27*

3. Attach the 24 inch zip tie to the wireguide mounts. Manually move the bed up and down and make sure the wireguide doesn't run into anything. The zip tie should maintain a graceful arc at all points and should naturally stay level with the 2020 extrusion (See Fig 18.29 and 18.30). **The teeth should be on the outside of the loop.**

    \
    *fig 18.28*

    \
    *fig 18.29*

    \
    *fig 18.30*

4. Trim the zip tie, once your happy with it's movement, and tighten the M3 screws to clamp it in place. *Mine was 520mm long when trimmed.*

    \
    *fig 18.31*

5. Attach the 8x wireguide loops to the 24" zip tie. There are teeth on the loops that should grab the teeth on the zip tie.

    \
    *fig 18.32*

6. Attach the bed to the frame using 4x bed leveling assemblies. Each assembly is as follows: M4 40mm flat head screw->M4 washer->bed spring->M4 washer->bed mount->bed leveling knob. **It's much easier to do this if you lay the printer frame on its side**

    \
    *fig 18.33*

    \
    *fig 18.34*

    Note: I used a chopstick to keep the M4 Nut in place. 

    \
    *fig 18.35*

7. Attach the heated bed wiring harness and thread it through the wire guide.

    \
    *fig 18.36*

8. Using small zip ties attach the heated bed wiring harness to the mounts and the loops to the large zip tie.

    \
    *fig 18.37*

9. Here's what it should look like when it's done.

    \
    *fig 18.38*

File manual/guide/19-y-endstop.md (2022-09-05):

# My BLV MGN Cube - Step 19 Mount Y Endstop

## [Step 19 BoM Spreadsheet Link](https://docs.google.com/spreadsheets/d/e/2PACX-1vTVx7BvB3V7CozF2l4eWkNntWrHSjOawmrsi_bRSVxQLIGVlfZTYEGp8a6fHpENV6hV2cn9PrDLHHl0/pubhtml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)

### Prep

1. Solder 45cm lengths of black and green wires onto the limit switch. The black wire should attach to the Common (COM) terminal and the green wire should attach to the Normally Closed (NC) terminal. *It's important to use NC instead of NO. If a wire breaks it will automatically trigger the endstop*

    \
    *fig 19.1*

2. Test the limit switch and wiring using the continuity tester on your Multimeter. It should be a closed circuit until you press the switch.

    \
    *fig 19.2*

### Assembly
1. Attach the Limit switch to 3d printed Y-Endstop-for-kw11-3p mount using the 2x M2 12mm screws. *Pretend these are socket head screws instead of star/phillips heads. It's just what I had handy*

    \
    *fig 19.3*

2. Attach the Y endstop mount to the frame as shown using 2x M5 10mm Screws and T-nuts (Fig 19.3). Positon it so that the switch is triggered just at the nozzle reaches the end of the bed and before it hits the bed power connector (Fig 19.4).

    \
    *fig 19.3*

    \
    *fig 19.4*

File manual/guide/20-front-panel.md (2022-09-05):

# My BLV MGN Cube - Step 20 Build Front Panel

## [Step 20 BoM Spreadsheet Link](https://docs.google.com/spreadsheets/d/e/2PACX-1vTVx7BvB3V7CozF2l4eWkNntWrHSjOawmrsi_bRSVxQLIGVlfZTYEGp8a6fHpENV6hV2cn9PrDLHHl0/pubhtml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)

### Prep

1. Adapt the EXP1 (10pin IDC) cable to use Ethernet extensions (For legacy LCD support)

    1. Cut the EXP1 ribbon cable about 60mm from each end and separate the ribbons into individual wires.

        \
        *fig 20.1*

    2. For the adapter that will attach to the TFT touch screen (Key on top of connector), splice with a keystone jack. Red wire is wire 1. Wires 6/7/8 are not used for EXP1 and can be trimmed.

        \
        *fig 20.2*

        Note: I used a stripper/puch down tool to make sure each wire was spliced properly. One of those plastic puch down tools, that usually comes with keystone jacks, would be fine but the ones I bought didn't come with them (That's what you get for $1/each).

        <details><summary>EXP1 Pinout</summary>
        <p>

        

        [Pinout Reference](https://reprap.org/wiki/RepRapDiscount_Full_Graphic_Smart_Controller)

        </p>
        </details>

    3. For the adapter that will attach to the controller board (Key on bottom connector), flip the cable over so red wire is on the left. Wiring is exactly the same as the LCD end. Wires 6/7/8 are not used for EXP1 and can be trimmed.

        \
        *fig 20.3*

    4. Make sure to attach the little caps on the keystones. These prevent the spliced wires from slipping out. Also it's a good idea to label the connectors with "EXP1". The Exp1 and Exp2 cables will **not** be interchangeable.

        \
        *fig 20.4*

1. Adapt the EXP2 (10pin IDC) cable to use Ethernet extensions (For legacy LCD support)

     2. Follow the same process you used for the EXP1 cable but with wires 7 and 10 not attached.

        \
        *fig 20.5*

        <details><summary>EXP2 Pinout</summary>
        <p>

        

        [Pinout Reference](https://reprap.org/wiki/RepRapDiscount_Full_Graphic_Smart_Controller)

        </p>
        </details>

1. Adapt RS232 (5pin JST-XH) cable to use Ethernet extensions (For TFT support)

    1. Using the RS232 (Black) cable provided with the TFT touch screen and 2 keystone jacks, make ethernet adapters (See picture for pinout). You will also need to replace the dupont connector with a 5 pin JST-XH connector (White). Note that the cable is a cross over cable with the pins reversed on each side.

	    \
        *fig 20.6*

        <details><summary>RS232 Pinout</summary>
        <p>

        

        </p>
        </details>

    2. Make sure to attach the little caps on the keystones. These prevent the spliced wires from slipping out. Also it's a good idea to label the connectors.

	    \
        *fig 20.7*

### Assembly
1. Using 2 Main jigs postion the 576mm 2020 extrusion 45mm above the lower front 4040 extrusion. Attach the extrusion to the front vertical extrusions using 4x angle brackets and 8x 8mm M5 screws/T-Nuts (2 brackets on each side).

    \
    *fig 20.8*

    \
    *fig 20.9*

2. Plug the EXP1, EXP2, and RS232 adapters into the back of the TFT touch screen.

    \
    *fig 20.10*

3. Using 4x M3 6mm screws attach the TFT touch screen to the TFT35 Mount.

    \
    *fig 20.11*

4. Using 4x M3 12mm screws attach the TFT35 Mount to the left panel.

    \
    *fig 20.12*

5. Attach the knob onto the TFT touch screen encoder.

    \
    *fig 20.13*

6. Attach 2x M5 10mm screws/T-Nuts to the left panel and attach to the frame as shown.

    \
    *fig 20.14*

7. Don't bother using the M5 attachment point inside the left panel. It's a pain to get to and you won't be able to adjust the panels later if you use it.

    \
    *fig 20.15*

8. Secure the bottom of the left panel using a M5 10mm screw/T-nut. Be careful because this part of the print is delicate. I broke it and had to fix it with crazy glue gel. To help position the T-nut use a strip of blue tape.

    \
    *fig 20.16*

    \
    *fig 20.17*

9. Attach 2x M5 10mm screws/T-Nuts to the center panel and attach to the frame as shown.

    \
    *fig 20.18*

    \
    *fig 20.19*

10. Using a M3 16mm screw and nut, tie the left and center panels together.

    \
    *fig 20.20*

11. Attach 4x M5 10mm screws/T-Nuts to the right panel.

    \
    *fig 20.21*

12. Carefully flex the panel to get the top T-Nuts into the 2040 extrusion channel and tighten.

    \
    *fig 20.22*

    \
    *fig 20.23*

13. Adjust the panels to close any gaps. I had to shift the left and right panels together to minimize the gaps.

    \
    *fig 20.24*

14. Attach the bottom of the right panel using a M5 10mm screw/T-Nut.

    \
    *fig 20.25*

15. Useing 4x M5 10mm screws/T-Nuts to attach the left and right grills to the bottom extrusion.

    \
    *fig 20.26*

    \
    *fig 20.27*

16. Here's what the front panel should look like at this point.

    \
    *fig 20.28*

17. Now attach 5 vertical wire mounts to the lower left side extrusion as shown.

    \
    *fig 20.29*

18. Connect the 3 Ethernet cables to the 3 Ethernet adapters in the panel and zip tie to the vertical wire mounts. *Attach the other end of each cable to their correspoinding adapters to avoid mixing them up.*

    \
    *fig 20.30*

19. Here's what it should look like when everything is done.

    \
    *fig 20.31*

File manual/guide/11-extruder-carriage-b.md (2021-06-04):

# My BLV MGN Cube - Assembly Instructions

## Step 11 Finish Building Extruder Carriage

### Step 11 BoM

#### Hardware
| Parts | Quantity | Details | Example Links |
|---|:---:|---|---|
| M2 15mm Philips Pan Head Screws | 2 | DIN7985 | |
| M2 Nuts | 3 | DIN934 | |
| M3 10mm Socket Head Cap Screws | 2 | DIN912 | |
| M3 14mm Socket Head Cap Screws | 2 | DIN912 | |
| M3 18mm Socket Head Cap Screws | 4 | DIN912 | |
| M3 25mm Socket Head Cap Screws | 2 | DIN912 | |
| M3 30mm Socket Head Cap Screws | 2 | DIN912 | |
| M3 Lock Nut | 1 | DIN934 | |
| M3 Washers | 4 | DIN125 | |
| Black Wire | ~15cm | 22 AWG Stranded Silicone | [Amazon](https://amzn.to/3ruTli7) |
| Green Wire | ~15cm | 22 AWG Stranded Silicone | [Amazon](https://amzn.to/3ruTli7) |
| Limit Switch | 1 | 3P with handle | [Aliexpress](https://s.click.aliexpress.com/e/_A4VObA) |
| Heat Shrink Tubing | 10mm | Enough to cover 3 Pins <BR>of a JST-XH Male Connector | |
| Male 3 Pin JST-XH Connector | 1 | Your controller uses these and you should too | [Aliexpress](https://s.click.aliexpress.com/e/_AWPLkY) [Amazon](https://amzn.to/3u0TiMD) |
| 3mm x 10.16cm zip ties (4in)  | 1-9 | ~2.5mm x ~120mm | [Amazon](https://amzn.to/3p2nDaE) |
| 5015 Blower Fan | 1 | 24V Ball Bearings | [Aliexpress](https://s.click.aliexpress.com/e/_A9XEXg) |
| V6 Hotend | 1 | Trianglelab V6 All-metal Hotend (1.75 24V All-metal) | [Aliexpress](https://s.click.aliexpress.com/e/_A7ETNG) |
| E3D Thermistor | 1 | Optional: I choose to give a little back to E3D.<br>Also it's super reliable/accurate | [Amazon](https://amzn.to/2QR6fdy) |
| 4010 Fan | 1 | 24V 2Pin Dual Ball Bearing | [Aliexpress](https://s.click.aliexpress.com/e/_A3DGg2) |
| BLTouch Probe | 1 | V3.1 is what I used | [Amazon](https://amzn.to/3rKZEhH) |
| PTFE Tubing | 1m |  1.9mm ID 4mm OD Capricorn Clone W/Cutter | [Aliexpress](https://s.click.aliexpress.com/e/_Anh45s) |
| 3mm x 10.16cm zip ties (4in)  | 2 | ~2.5mm x ~120mm | [Amazon](https://amzn.to/3p2nDaE) |

#### Printed Parts
| Parts | Quantity | Details |
|---|:---:|---|
| [X_carriage_-_modified_MK3_fan_blower.stl](../../parts/source/stl/X_carriage_-_modified_MK3_fan_blower.stl) | 1 | [Printed Parts Settings](../partsSettings.md) |
| [X_carriage_-_Fan_mount.stl](../../parts/source/stl/X_carriage_-_Fan_mount.stl) | 1 | [Printed Parts Settings](../partsSettings.md) |
| [X_carriage_-_V6_Locker_BL-touch.stl](../../parts/source/stl/X_carriage_-_V6_Locker_BL-touch.stl) | 1 | [Printed Parts Settings](../partsSettings.md) |
| [X_carriage_-_Cable_locker_JSR.stl](../../parts/remixed/X_carriage_-_Cable_locker_JSR.stl) | 1 | [Printed Parts Settings](../partsSettings.md) |
| [X_carriage_-_Block_shield_for_Bltouch-8mm-12mm_sensors.stl](../../parts/source/stl/X_carriage_-_Block_shield_for_Bltouch-8mm-12mm_sensors.stl) | 1 | [Printed Parts Settings](../partsSettings.md) |

#### Tools
| Parts | Quantity | Details | Example Links |
|---|:---:|---|---|
| Soldering Iron and Solder | 1 | For small electronics | [Amazon](https://amzn.to/3rvsgLI) |
| Multimeter W/Continuity Tester | 1 | This multimeter has a temp probe too! | [Amazon](https://amzn.to/3sxUjeT) |
| Threadlocker | 0.2 Fl. Oz | Blue (removable) formula | [Amazon](https://amzn.to/3w539Tr) |
| M3 Screwdriver | 1 | | [Amazon](https://amzn.to/3qNmEgs) |
| Small Philips Screwdriver |1 | | [Amazon](https://amzn.to/3fDZgyZ) |
| 5.5 Hex wrench | 1 | Or Pliers | [Amazon](https://amzn.to/3bqH73V) |
| Butane Mini Torch | 1 | You might need to purchase ligher fluid separately (Can't remember) | [Amazon](https://amzn.to/2R3ymGG) |

### Prep

1. Solder 15cm lengths of black and green wires onto the limit switch. The black wire should attach to the Common (COM) terminal and the green wire should attach to the Normally Closed (NC) terminal. *It's important to use NC instead of NO. If a wire breaks it will automatically trigger the endstop*

    \
    *fig 11.1*

2. Test the limit switch and wiring using the continuity tester on your Multimeter. It should be a closed circuit until you press the switch. *Throughout the wiring of the switch you should check this*

    \
    *fig 11.2*

3. Make sure the heater cartridge and thermistor wires come out this side of the heater block.

    \
    *fig 11.3*

4. Route the 4010 Fan and BLTouch Probe wires through the bottom of the X Carriage Cable Locker and temporarly secure with a zip tie. Make sure to stay to the right of the bottom cross bar.

    \
    *fig 11.4*

### Assembly
1. Remove the 2 lower M3 40mm Socket Head Cap Screws/Nuts from the X carrage and remove the bottom of the carriage. *Belts should be a little loose so it doesn't stress the rest of the carriage*

    \
    *fig 11.5*

2. Dip the ends of the 2 M2 15mm Philips Pan Head Screws in threadlocker.

    \
    *fig 11.6*

3. Insert the 2 M2 15mm screws in to the lower X carrage as shown. You'll notice that I snapped off the bridge on this piece and I'm using M2's instead of M2.5s. This works much better, in reality, than what's described in BLV's extruder assembly video.

    \
    *fig 11.7*

4. Attach the limit switch to the lower X carrage using the M2 screws and nuts. You may need to file down the sides of the carraige to get the switch to fit. Don't overtighted the screws as the switch is delicate and you can crush the hollow casing. Note how I routed the wires.

    \
    *fig 11.8*

5.  Insert an M3 nuts into the fan blower as shown. *Don't worry about the other hole*

    \
    *fig 11.9*

6. Using the M3 14mm Socket Head Cap Screw, attach the fan blower to the lower X carriage.

    \
    *fig 11.10*

7. Put 10mm of heat shrink tubing over both wires and then solder the wires as shown. Then slide the tubing over the exposed terminals of the male JST connector and apply heat to the shrink the tubing with the Mini Butane Torch.

    \
    *fig 11.11*

    \
    *fig 11.12*

    \
    *fig 11.13*

8. Reattach the lower X carriage to the rest of the X carriage using the M3 40mm screws/nuts. *I used some threadlocker on the nuts for good measure*

    \
    *fig 11.14*

9. Zip tie the limit switch wiring to the back X carriage.

    \
    *fig 11.15*

10. Cleanup and trim the belts. Now is a good time to trim your belts and verify the limit switch can trigger without the belts catching in the idlers. *I also had to redo some of my zip ties so I could trim the belts closer*

    \
    *fig 11.16*

11. Insert the 2 M3 25mm Socket Head Cap Screws, with washers, into the 5015 blower fan.

    \
    *fig 11.17*

12. Put the Fan mount over the screw ends.

    \
    *fig 11.18*

13. Secure the screw closest to the blower opening with a lock nut. *Don't overtighten or you will damage the fan*

    \
    *fig 11.19*

14. Attach the blower fan to the X carraige and blower duct. Make sure the mouth of the blower is inserted into the duct correctly. *Don't overtighten or you will damage the fan*

    \
    *fig 11.20*

15. Secure the blower fan wores and limit switch wires with a zip tie to the mount point on the back x carrage plate. Leave a little slack on the blower wire but make sure it doesn't run into the linear rail mount when the carriage is all the way to the left. *You should have a little more slack for the limit switch connecter than what you see in this pic. I updated the directions after realizing it was too short*

    \
    *fig 11.21*

16. Attach the Hotend to the X Carrage.

    \
    *fig 11.22*

17. Attach the PTFE tubing to the hotend and then secure the hotend using the BLTouch Locker and 2 M3 30mm Socket Head Cap Screws. *To insert the tubing into the hotend, remove the orange clip and press down on the fitting then reattach the clip to secure it.*

    \
    *fig 11.23*

18. Connect the cable locker using the M3 14mm Socket Head Cap Screw. Make sure it grabs the nut embedded in the X carriage. If the screw bottoms out before it's tight use some M3 washers. The orientation of the cable locker is important. The bumps/lower offset should point towards the front.

    \
    *fig 11.24*

19. Using the 2 M3 10mm Socket Head Cap Screws and nuts and washers. Secure the BLTouch to the locker mount. Make sure the BLTouch probe is secure but don't overtighten or you might damage it.

    \
    *fig 11.25*

20. Using the 4x M3 18mm Socket Head Cap Screws attach the Block Sheild to the front of the X carriage. Make sure the 4010 fan is oriented so it will blow air across the heat sink. Also route the BLTouch probe wires inside the Block Sheild making sure not to pinch them.

    \
    *fig 11.26*

    \
    *fig 11.27*

    \
    *fig 11.28*

    \
    *fig 11.29*

    \
    *fig 11.30*

21. Now route and zip tie the heater cartridge and thermistor wires so they are out of the way.

    \
    *fig 11.31*

22. Here's what it should look like when everything is done.

    \
    *fig 11.32*

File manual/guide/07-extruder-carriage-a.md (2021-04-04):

# My BLV MGN Cube - Assembly Instructions

## Step 7 Partially Build Extruder Carraige

### Step 7 BoM

#### Hardware
| Parts | Quantity | Details | Example Links |
|---|:---:|---|---|
| M3 10mm Socket Head Cap Screws | 4 | DIN912 | |
| M3 40mm Socket Head Cap Screws | 4 | DIN912 | |
| M3 Nuts | 10 | DIN934 | |

#### Printed Parts
| Parts | Quantity | Details |
|---|:---:|---|
| X_carriage_-_Bottom.stl | 1 | [Printed Parts Settings](../partsSettings) |
| X_carriage_-_Top.stl | 1 | [Printed Parts Settings](../partsSettings) |
| X_carriage_-_Front_plate.stl | 1 | [Printed Parts Settings](../partsSettings) |
| X_carriage_-_Rear_plate.stl | 1 | [Printed Parts Settings](../partsSettings) |

#### Tools
| Parts | Quantity | Details | Example Links |
|---|:---:|---|---|
| M3 Screwdriver | 1 | | [Amazon](https://amzn.to/3qNmEgs) |
| 5.5 Hex wrench | 1 | Or Pliers | [Amazon](https://amzn.to/3bqH73V) |
| Blue Tape | 1 roll | | [Amazon](https://amzn.to/3ujyctH) |

### Prep
1. Clean support material out of any nut traps and holes.

    \
    *fig 7.1*

### Assembly
1. Prepare the x carrage top by inserting an M3 nut in the nut trap on the underside.

    \
    *fig 7.2*

1. Attach the X carriage top to the X linear rail with the 4 M3 x 10mm screws. *The top carriage isn't perfectly symmetrical so make sure that it is flush or overhangs the sides of the linear rail carriage*

    \
    *fig 7.3*

2. Prepare the front plate by inserting 2 of the M3 40mm screws and 4 of the M3 nuts into the nut traps. If the nuts are loose, use blue tape temporarily secure them.

    \
    *fig 7.4*

    \
    *fig 7.5*

3. Now carefully attach the front plate to the top plate by inserting the M3 40mm screws through the top plate thru holes.

    \
    *fig 7.6*

4. Prepare the back plate by inserting an M3 nut into the nut trap. *If it's loose secure it with blue tape*

    \
    *fig 7.7*

    \
    *fig 7.8*

5. Attach the back plate to the top plate.

    \
    *fig 7.9*

6. Hand tighten 2 M3 nuts onto the ends of the M3 40mm screws. Then carefully remove the blue tape you used to hold the nuts in place. They should now be held captive by the linear carriage and top carriage.

    \
    *fig 7.10*

    \
    *fig 7.11*

7. Finish tightening the nuts using the hex wrech and M3 screw driver.

    \
    *fig 7.12*

8. Using the remaining 2 M3 x 40mm screws secure the bottom plate by sandwitching it between the front and back plates. *You'll be removing the bottom plate in a later step do don't worry about attaching switches or the correct orientation.*

    \
    *fig 7.13*

    \
    *fig 7.14*

9. Here is what you should have when you are done. We just need enough to secure the belts. We'll do the rest later

    \
    *fig 7.15*

    \
    *fig 7.16*

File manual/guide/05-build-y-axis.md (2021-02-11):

# My BLV MGN Cube - Assembly Instructions

## Step 5 Build Y Axis

### Step 5 BoM

#### Hardware
| Parts | Quantity | Details | Example Links |
|---|:---:|---|---|
| M5 16mm Socket Button Head Screws | 2 | DIN9427 (Or M5 15mm) | |
| M5 10mm Socket Button Head Screws | 6 | DIN9427 | |
| M5 T-Nuts | 8 | Hammer Head/Drop In Style | |
| M3 T-Nuts | 9 | Hammer Head/Drop In Style | |
| M3 8mm Socket Head Cap Screws | 9 | DIN912 | |
| M3 0.7~1mm washer | 12 | | |
| M3 35mm Socket Head Cap Screws | 4 | DIN912 | |
| M3 50mm Socket Head Cap Screws | 4 | DIN912 | |
| 623zz Flanged Bearing | 8 | |
| M3 Thin Square Nut | 4 | DIN562 | [Amazon](https://amzn.to/2MPCNTI) |
| M3 Lock Nut | 2 | |
| MGN12H 400mm Linear Rail | 1 | Quality ... Meh... | [Aliexpress](https://www.aliexpress.com/item/32829826159.html?spm=a2g0s.9042311.0.0.27424c4dwPelhS) |
| 460mm (~18in) 2020 extrusion | 1 | From standard 365mm Z frame |
| 3mm x 10.16cm zip ties (4in)  | 4-8 | ~2.5mm x ~120mm | [Amazon](https://amzn.to/3p2nDaE) |

#### Printed Parts
| Parts | Quantity | Details |
|---|:---:|---|
| X_mount_-_Top_left.stl | 1 | [Printed Parts Settings](../partsSettings) |
| X_mount_-_Top_right.stl | 1 | [Printed Parts Settings](../partsSettings) |
| 2020_Jig.stl | 2 | [Printed Parts Settings](../partsSettings) |

#### Tools
| Parts | Quantity | Details | Example Links |
|---|:---:|---|---|
| Needle Files | 1 set | | [Amazon](https://amzn.to/3cTLQgR) |
| M5 ball end tip screwdriver | 1 | Especially helpfull working with the brackets | [Amazon](https://amzn.to/36TSnEy) |
| M3 screwdriver | 1 | | |
| Build plate | 1 | Used to square the X beam | |

### Prep
1. Install M5 8mm screws and T-nuts in the top blocks.

    \
    *fig 5.1*

2. Clean the nut traps and holes on the lower blocks using the needle files.

    \
    *fig 5.2*

    \
    *fig 5.3*

### Assembly

1. Attach M5 16mm screws and M5 8mm screws with T-Nuts to both left and right lower blocks

    \
    *fig 5.4*

2. Place the 460mm 2020 extrusion on top of the lower blocks. *should be a tight fit but still allow the rails to slide freely*

    \
    *fig 5.5*

3. Use Zip Ties to attach the build plate into the channel of the 2020 extrusion and channel of the back 2040 extrusion. *This is used to keep the 2020 extrusion perfectly parallel to the back 2040 extrusion*

    \
    *fig 5.5*

4. Tighten the lower block M5 10mm Screws and T-Nuts to firmly attach them to the 2020 extrusion. *Do this on both sides*

    \
    *fig 5.6*

5. Prepare the 2 bearing stacks for assembly. You'll be making a sandwich of washers and bearings. (washer->bottom flanged bearing->washer->top flanged bearing->washer)

    \
    *fig 5.7*

6. Insert the 2x M3 35mm screws into the left upper block and assemble the bearing stacks on them. *If you have particularly skinny washers (0.5mm) you should double them to make 1mm*

    \
    *fig 5.8*

7. While holding the bearing stack, flip the left upper block and slide the attached M3 35mm screws into the corresponding holes in the left lower block. **Don't insert M3's all the way as you still need to put nuts in the bottom block nut traps**

    \
    *fig 5.9*

    \
    *fig 5.10*

8. Slide the M3 thin square nuts into the nut traps for the M3 35mm screws and then tighten them until they catch the nuts. Also insert the M3 50mm screw in the center hole. *Don't tighten any of the screws all the way down yet.

    \
    *fig 5.11*

9. Tighten M5 10mm and M5 16mm screws and T-Nuts in the left upper block into the 2020 extrusion.

    \
    *fig 5.12*

10. Attach the M3 lock nut to the bottom of the M3 50mm screw and tighten it along with the 2x M3 35mm screws.

    \
    *fig 5.13*

13. Repeat the instruction above to complete the right side. *See below for completed view*

    \
    *fig 5.14*

14. Remove build plate you used to keep things square.

    \
    *fig 5.14*

15. Check bearings for free movement. Also check to make sure 2020 extrusion can slide forward and back smoothly on the linear rails. *careful not to slide carriages off of rails*

16. Attach 9x M3 8mm screws and M3 T-Nuts onto the 400mm linear rail.

    \
    *fig 5.15*

17. Install the linear rail onto the top of the 2020 extrusion and attach the 2x 2020 jigs. *make sure the rail is centered between the left and right pulley blocks*

    \
    *fig 5.16*

18. If the 2020 jigs are loose on the 2020 extrusion or allow any play on the linear rail, apply tape to **both** sides of the jig to improve the fit while still keeping it centered. Also make sure to poke a hole so you can tighten the M3 screws with the jig in place.

    \
    *fig 5.17*

19. Starting in the middle of the rail alternate tightening the M3 screws. Work your way to the ends on either side, moving the guides outward and tightening as you go.

    \
    *fig 5.18*

    \
    *fig 5.19*

20. You should now have a perfectly aligned X rail on smoothly sliding y rails.

    \
    *fig 5.20*

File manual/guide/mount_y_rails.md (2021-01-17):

# My BLV MGN Cube

## Assembly Instructions

### Step 1

#### Parts

* 18x M3 T-Nuts
* 26x M3 8mm socket head cap screws
* 2x 496mm (19.5in) 2040 extrusions
* 2x 400mm linear rails
* 2x 2040 Jigs (2040_Jig.stl)
* 1x Left bottom X mount (X_mount_-_Bottom_left.stl)
* 1x Right bottom X mount (X_mount_-_Bottom_right.stl)

#### Assembly

1. Attach T-Nuts into every other hole of linear rail using M3 8mm socket head cap screws (See Fig 1.1). If there is an extra hole just double up at the end. Be careful not to let the carriages fall off the linear rails.
    
    \
    *fig 1.1*

2. Mount a rail on one of the 2040 extrusions and center over the left channel using the two 2040 jigs to properly center it (See Fig 1.2).

    \
    *fig 1.2*

1. If your jigs are a little loose you can use some tape placed equally on both sides to tighten them up (See Fig 1.2b). (See Fig 1.2b).

    \
    *fig 1.2b*

1. Offset the top of the rail by 70mm (See Fig 1.3). This is because the pulleys at the back of the printer take up more space than the tensioner at the front.

    \
    *fig 1.3*

1. Tighten the T-Nuts using the guides to make sure the linear rail remains centered over the channel (See Fig 1.4)

    \
    *fig 1.4*

1. Attach the left bottom X mount to the linear rail using 4x M3 8mm screws (See Fig 1.5).

    \
    *fig 1.5*

1. Repeat the above steps to complete the right rail.

2. Here is what it should look like when you are done (See Fig 1.6)

    \
    *fig 1.6*

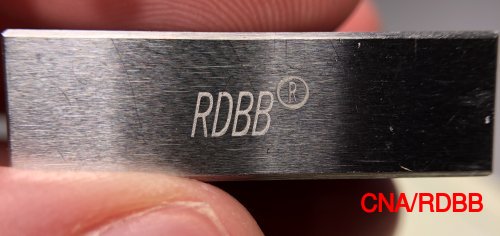
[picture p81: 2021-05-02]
notes/img/CNAManufacturer.JPG

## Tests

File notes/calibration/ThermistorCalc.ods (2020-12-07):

ADC Voltage | Temp
993 | 16 | New
986 | 20 | New
897 | 50 | New
229.5 | 132
230 | 152 | New
189 | 141
155 | 150
128 | 159
105.94 | 169
87 | 177
73 | 185
117 | 188 | New
61 | 194
51 | 202
43 | 210
37 | 217
31 | 226
51 | 229 | New
29 | 230
34 | 252 | New
Temp
5
ADC Value
3,405
Exponential trendline formula is y=ae^bx

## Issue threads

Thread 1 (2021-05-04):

Add EU supplier for LDO Linear Bearings

jsaintrocc, 2021-05-04:
For the Linear Bearing bakeoff should add these guys to give our friends in the EU more options :-)

https://vrparts.de/.../ldo-linearschienen-mgn12h-1r-l-400mm

jsaintrocc, 2021-05-07:
Fixed

Closed 2021-05-07.

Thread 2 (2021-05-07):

Add Nut trap to bed mount

jsaintrocc, 2021-05-07:
The current bed mount should have a nut trap option so you can just adjust with the top hex.

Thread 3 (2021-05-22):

Missing 2 M3x10 mm in step 8?

marutter, 2021-05-22:
I believe in both back corners, there is a place to attach the stepper motor to the corner block with a M3x10mm.  Best to install them before the belts, I think.

Great set of pages.  Referencing them all the time while building my own MGN Cube.

jsaintrocc, 2021-05-23:
Hi @marutter thanks for the feedback!

I can't figure out where the 2 M3x10mm would attach to the steppers in [Step 8 Partially Build Back Corners](https://github.com/jsaintrocc/myblvmgncube/blob/master/manual/guide/08-back-corners-a.md). In fig 8.17 (Substep 11) we temporarily attach them using 2 M3x35mm. Which figure would be closest to where they should go?

~James

marutter, 2021-05-23:
In figure 8.6, up an to the right of the second arrow there is a 3mm hole countersunk for the socket head of a M3.  I don't think you refer to that location in the rest of the assembly instructions.

jsaintrocc, 2021-05-23:
Yup. Sure enough. I just pulled apart my left back corner and I completely missed it. Looks like an M3x8mm will be more in line with the other 3 screws. They only go about 3mm into the stepper. I'll add that to the instructions. Good catch!

jsaintrocc, 2021-05-23:
OK. Added the missing screws in Commit: f75bb6edfb0c274f0bd16ca5e63dc5460b07fc54

Closed 2021-05-23.

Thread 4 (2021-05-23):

Better way to align bed frame holder

jsaintrocc, 2021-05-23:
The Left and right bed frame holders need to be centered on the bed frame but lack any center mark on the part. Also consider designing a guide to make sure they are centered relative to one another. It's actually not as important that they're exactly centered as much as they are both in the same distance from one edge of the longer extrusion.

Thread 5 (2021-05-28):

Consider Better Cable Management Strategy

jsaintrocc, 2021-05-28:
Maybe use 22AWG ethernet cables and a centralized connecter on hotend and chassis for easy replacability. Also Toms got some good suggestions here: https://youtu.be/ZPWoC3N0epM.

Also the conduit is probably the best solution barring going to drag chains which is probably overengineerd for what we're trying to do.

jsaintrocc, 2021-09-15:
Maybe try adapting the bed cable management system for the hotend. This should be minimalist and light weight.

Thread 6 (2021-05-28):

Modify cable lockers on Hotend and frame to properly handle 13mm ID conduit.

jsaintrocc, 2021-05-28:
Lockers are different sizes from one another and neither fits a 13mm ID and 16mm OD conduit well. Do the minimum mod necessary to  these parts to make them work.

jsaintrocc, 2021-08-20:
Completed the redesign in Step 17.

Closed 2021-08-20.

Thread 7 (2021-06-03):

Redesign the hotend grill to be easier to print

jsaintrocc, 2021-06-03:
The long grill lines and the fillets on the edges make this really challenging to print. Maybe go to a hex patter and clean up the connections with the edges.

jsaintrocc, 2021-06-03:
Also remove the dependency on the cable locker and make a slot instead of a hole for the bowden tube.

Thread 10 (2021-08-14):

Missing Y-endstop

marutter, 2021-08-14:
I just finished assembling my Cube through your step 14.  Your instructions have been amazing, thank you.

One thing I think you are missing is the Y endstop (part Y_Endstop_-_Front_Left_-_Rear_left).  Not sure if you are going to add that in a later step, or if should be added to step 12 and then adjusted later.

jsaintrocc, 2021-08-16:
Thanks @marutter. Good catch! I was debating where to put that but I like your suggestion of putting it in step 12 since it attaches to one of those cross beams. I'm add it once I'm done with my current step which is the cable management and extruder mounting for the hotend.

Regarding the 3d printed piece. Did you need to modify it at all too attach the switch? The holes look really small compared to the limit switch.

Thanks, James

jsaintrocc, 2021-08-16:
Did a quick test fit. Looks like M2 12mm screws w/washers will do but the 3d parts holes don't line up with switch.

jsaintrocc, 2021-08-17:
See Fysetc's [video](https://www.youtube.com/watch?v=KnPkUY0QOnw) at 16:18 to see how they did it.

jsaintrocc, 2021-09-13:
Ready to go just blocked by heated bed assembly.

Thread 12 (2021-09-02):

Create Cable Management System for Heated Bed Wires

jsaintrocc, 2021-09-02:
Need to create a cable management system to keep the wires from getting tangled and to maintain the proper bend radiuses. Also need keep them well ventilated as they are high amperage.

jsaintrocc, 2021-09-02:
notes from last interation:

- Add 1mm gap between M5 bolts and central armature for clearance
- Reposition nut trap by .5mm to allow for bridging for large zip tie hole
- Add extrusion channel guide to extrusion mount
- Reinforce extrusion mount and make more 3d printable by adding 45 degree reinforcements
- Print wire clamp in same orientation as main part
- Redesign wire clamp with less bevels for zip ties (if you can print in the right orientation)

Closed 2021-10-05.

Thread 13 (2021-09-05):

Document Controller Boards Installation and Wiring

jsaintrocc, 2021-09-05:
- Install the SKR 1.4 Turbo
- Install the Heated Bed MOSFET
- Install the Raspberry Pi
- Wire everything up

jsaintrocc, 2022-02-20:
Modified this issue just to do the wiring and not the complete controller firmware setup and calibration. Would be too big an issue to include everything.

jsaintrocc, 2022-08-27:
#40 has resolved this issue.

Closed 2022-08-27.

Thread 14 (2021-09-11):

Add Shim to BLTouch Install

jsaintrocc, 2021-09-11:
The BLTouch sensor is too high using the standard mount and a V6 hotend. It needs a 2mm - 3mm shim.

Antlabs recommends a offset of between 2.3mm to 4.3mm from the nozzle tip [doc reference](https://5020dafe-17d8-4c4c-bf3b-914a8fdd5140.filesusr.com/ugd/f5a1c8_d40d077cf5c24918bd25b6524f649f11.pdf)

jsaintrocc, 2021-09-11:
You used 12mm M3 screws and a 2mm shim. Might want to go  to a 3mm shim instead as I think you're close to the top end of 4mm offset.

jsaintrocc, 2021-09-11:
Include directions on verifying this later. During your checkout procedure.

jsaintrocc, 2021-09-11:
This is the shim I used https://www.thingiverse.com/thing:3444787. Include that in our project.

jsaintrocc, 2022-09-26:
Instead of adding a shim. Just redesign this part.

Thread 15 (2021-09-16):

Fix all the broken stl links in the guide

jsaintrocc, 2021-09-16:
many of the stl files are missing the "parts" folder resulting in broken links.

jsaintrocc, 2022-09-05:
fixed with #39

Closed 2022-09-05.

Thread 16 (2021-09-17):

Revise Bed Spring Setup

jsaintrocc, 2021-09-17:
Consider buying this bed leveling kit and flipping the bed mounts in order to

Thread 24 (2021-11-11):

Fix broken plate vs bracket images

jsaintrocc, 2021-11-11:
It's missing the 'guide' in the URL

Closed 2022-09-05.

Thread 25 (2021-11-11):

Broken STL links

jsaintrocc, 2021-11-11:
Noticed that the Main Jig links are broken. Probably need to update other early instructions as well.

jsaintrocc, 2021-11-11:
It's only and issue in the Bom because of relative links.

jsaintrocc, 2022-09-05:
Duplicate fixed in #15

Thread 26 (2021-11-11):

Review and adapt BLV klipper instructions

jsaintrocc, 2021-11-11:
https://www.blvprojects.com/post/klipper-ultra-fast-printing-9000acc-500mm-s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

jsaintrocc, 2021-11-20:
Also consider the superslicer fork that BLV is using.

jsaintrocc, 2021-11-20:
Here is Ben's klipper config for reference: [BLV printer cfg.zip](https://github.com/jsaintrocc/myblvmgncube/files/7575025/BLV.printer.cfg.zip)

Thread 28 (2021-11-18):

Adding the wifi switch for Octoprint Power Control

jsaintrocc, 2021-11-18:
Using a wifi switch the printer can be controlled to both power on and off from octoprint.

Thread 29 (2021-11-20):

Redesign X endstop mount to allow better clearance

jsaintrocc, 2021-11-20:
Currently the X endstop triggers a fraction of a mm before the hotend runs into the mount. Putting the endstop flush with that side of the hotend would be better. Some switches have a wheel attached and that would add a little more clearance but why add the weight.

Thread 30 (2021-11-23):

Add instruction on squaring your X-axis against the front tensioners

jsaintrocc, 2021-11-23:
Got this idea from the [Voron Trident Addembly Manual](https://github.com/VoronDesign/Voron-Trident/blob/main/Manual/Assembly_Manual_Trident.pdf) page 118. It recommends squaring the x-axis against the back motors. In our setup it's easier to do it against the front tensioners.

Basically loosen the x-axis M5 bolts that secure it to the extrusion. Push it up against the front tensioners and hold there while your tighten them. Also when tensioning the belts hold against front tensioners to make sure you don't add any skew into the axis.

jsaintrocc, 2022-09-16:
Inspired by this belt gauge https://www.printables.com/model/135075-belt-tension-gauge#preview

jsaintrocc, 2022-09-16:
The Voron method is prone to all sorts of interference. The assumption is that plucking the string will produce a single clean frequency. This is a flawed assumption because, unlike a cartesian, the belt path is much more complex and the pulleys on both ends of the length of the belt being tested aren't fixed in place. This means the pulleys, X gantry, and X carriage could all interfere. A better method would be to measure belt deflection using a known weight. That weight will be a bottle of liquid that can accurately be measured with a kitchen scale.

jsaintrocc, 2022-09-17:
Also investigate this https://www.printables.com/model/190393-corexy-belt-tension-matcher

Closed 2022-09-24.

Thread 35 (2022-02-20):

Document Raspberry Pi/SKR Board Configuration

jsaintrocc, 2022-02-20:
Now that I have everything running well with Klipper I'll document that instead of Marlin.

- Flash the rPi
- Use the rPi to flash the SKR board
- Run through some preliminary testings to validate everything is working

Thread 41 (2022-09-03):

Add Controller Fan Mount Step to Step 21

jsaintrocc, 2022-09-03:
Missing step for attaching the Fan and adding to the din rail

jsaintrocc, 2022-09-26:
This will be resolved in PR #48.

Closed 2022-09-26.

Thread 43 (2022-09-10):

Try out the EVA extrudor

jsaintrocc, 2022-09-10:
Lots of support for BLV Cube and seems well supported and modular with step source files available.

https://pkucmus.github.io/EVA/

Here's one that looks like a drop in fit for BLV Cube w/V6 & Bowden

https://pkucmus.github.io/EVA/assemblies/bowden-mgn12corexyv6/

jsaintrocc, 2022-09-10:
Here's the contributed conversion kit for the BLV Cube 6mm belt setup:

https://contrib.eva-3d.page/printer-compatibility/blv-mgn-cube/

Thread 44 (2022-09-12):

Replace Extruder__-_bontech_Rear_mount.stl with a smaller alternate

jsaintrocc, 2022-09-12:
In step 15 you the old extruder mount as a template for drilling holes. You should replace this with something specialized as you don't use that part in the actual printer anymore

https://github.com/jsaintrocc/myblvmgncube/blob/master/manual/guide/15-electronics-panel.md

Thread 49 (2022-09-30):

Use Serial interface of BTT TFT via rPi

jsaintrocc, 2022-09-30:
Currently, you're using the 12864 LCD emulator for your TFT to work with Klipper. It's buggy and so 2010. You should be able to connect the TFT directly to the rPi using a cheap rs232 to USB adapter and use some serial virtualization code to enable 2 devices to write and read from the same serial port.

jsaintrocc, 2022-09-30:
One problem with having 2 devices use the same serial port is that the serial port is that read commands would only show up on whichever device reads it (buffer limitation) Here's a useful article on cloning a serial port:
https://unix.stackexchange.com/questions/12800/cloning-splitting-a-serial-port-com-port-in-ubuntu
and the referenced software project
https://github.com/danielinux/ttybus

jsaintrocc, 2022-09-30:
You will also need a USB to TTL/RS232 adapter. Aliexpress is $2 cheaper but no tracking and could take 2 months. Wen't with the amazon one as it's still under $10 and you'll get it tomorrow.

amazon:
https://www.amazon.com/HiLetgo-CP2102-Converter-Adapter-Downloader/dp/B00LODGRV8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
aliexpress
https://www.aliexpress.us/item/2255799934372737.html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

jsaintrocc, 2022-09-30:
This may also help
http://stackexchange.com/users/6463673/meuh

jsaintrocc, 2022-09-30:
Octoprints current serial settings:
port='/tmp/printer', baudrate=115200, bytesize=8, parity='N', stopbits=1, timeout=10.0, xonxoff=False, rtscts=False, dsrdtr=False), starting monitor

jsaintrocc, 2022-09-30:
This almost works accept cr isn't working
```
picocom /dev/pts/0 --baud 115200 --echo --noinit --noreset --nolock --omap crlf --imap crlf --emap crlf
```

jsaintrocc, 2022-10-01:
https://github.com/torfsen/python-systemd-tutorial

jsaintrocc, 2022-10-01:
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

Still need to fix the backspace

jsaintrocc, 2022-10-01:
This might work as well
https://www.youtube.com/watch?v=G7yqrAaUMPw

jsaintrocc, 2022-10-01:
With tty_bus use picocom with the following command line
```
picocom /tmp/printer0 --baud 115200 --echo --omap crlf --imap lfcrlf
```

jsaintrocc, 2022-10-01:
muxing the serial port is looking to be too much of a hack. ttymux doesn't seem to work with octoprint and I'm worried that octoprint and the screen messages on the same serial line are going to confuse one another.

A better approach is probably to create a octoprint plugin that talks to the screen and proxies the commands trough octoprint.

jsaintrocc, 2022-10-01:
Here are some example plugins that deal with serial and Gcode
https://plugins.octoprint.org/plugins/klipper/
https://github.com/OctoPrint/OctoPrint-FirmwareUpdater
https://plugins.octoprint.org/plugins/display_panel/

jsaintrocc, 2022-10-03:
rPI can supply a total of 1.2a on its USB ports. In testing the TFT35 2.0 drew 160ma so it shouldn't be a problem. Always make sure to use a quality power supply with the pi's.

Link for more details. (Search for "Power Supply")
https://www.raspberrypi.com/documentation/computers/raspberry-pi.html

jsaintrocc, 2022-10-09:
There is moonraker code to do this for panel due https://github.com/Arksine/moonraker/blob/master/moonraker/components/paneldue.py
According to some Voron folks paneldue does used gcode commands similar to BTT TFT35

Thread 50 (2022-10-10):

Add Fire Suppression System

jsaintrocc, 2022-10-10:
This will require an enclosure. "BlazeCut “T” Series System T050E" is the actual product

https://help.prusa3d.com/guide/5-fire-suppression-system-add-on_347566

USA distributor https://www.printedsolid.com/products/original-prusa-fire-suppression-system

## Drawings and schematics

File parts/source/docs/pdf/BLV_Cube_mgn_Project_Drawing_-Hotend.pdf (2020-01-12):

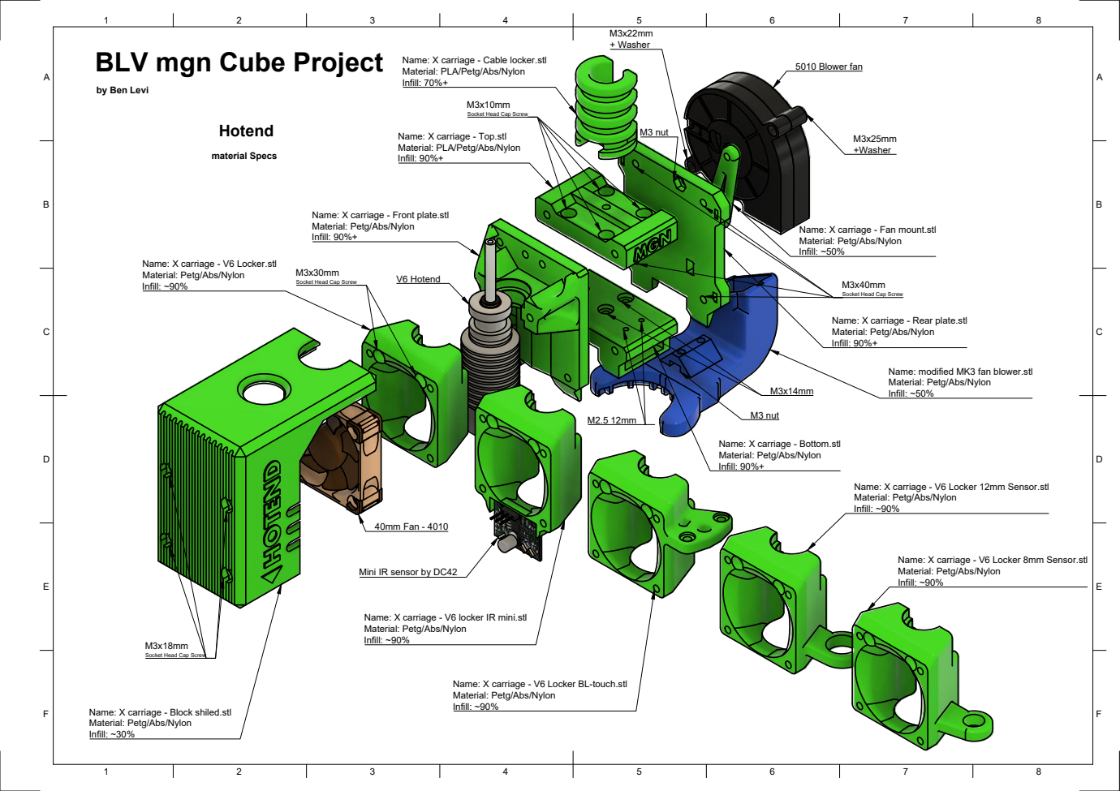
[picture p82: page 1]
material Specs; 40mm Fan - 4010; V6 Hotend; 5010 Blower fan; M3 nut; + Washer; M3 nut M2.5 12mm

BLV mgn Cube Project

Name: X carriage - Cable locker.stl
Material: PLA/Petg/Abs/Nylon
Infill: 70%+

by Ben Levi

Socket Head Cap Screw

Name: X carriage - Top.stl
Infill: 90%+

Name: X carriage - Front plate.stl
Material: Petg/Abs/Nylon

Name: X carriage - Fan mount.stl
Infill: ~50%

Name: X carriage - V6 Locker.stl
Infill: ~90%

Name: X carriage - Rear plate.stl

Name: modified MK3 fan blower.stl

Name: X carriage - Bottom.stl

Name: X carriage - V6 Locker 12mm Sensor.stl

Name: X carriage - V6 Locker 8mm Sensor.stl

Mini IR sensor by DC42

Name: X carriage - V6 locker IR mini.stl

Name: X carriage - V6 Locker BL-touch.stl

Name: X carriage - Block shiled.stl
Infill: ~30%

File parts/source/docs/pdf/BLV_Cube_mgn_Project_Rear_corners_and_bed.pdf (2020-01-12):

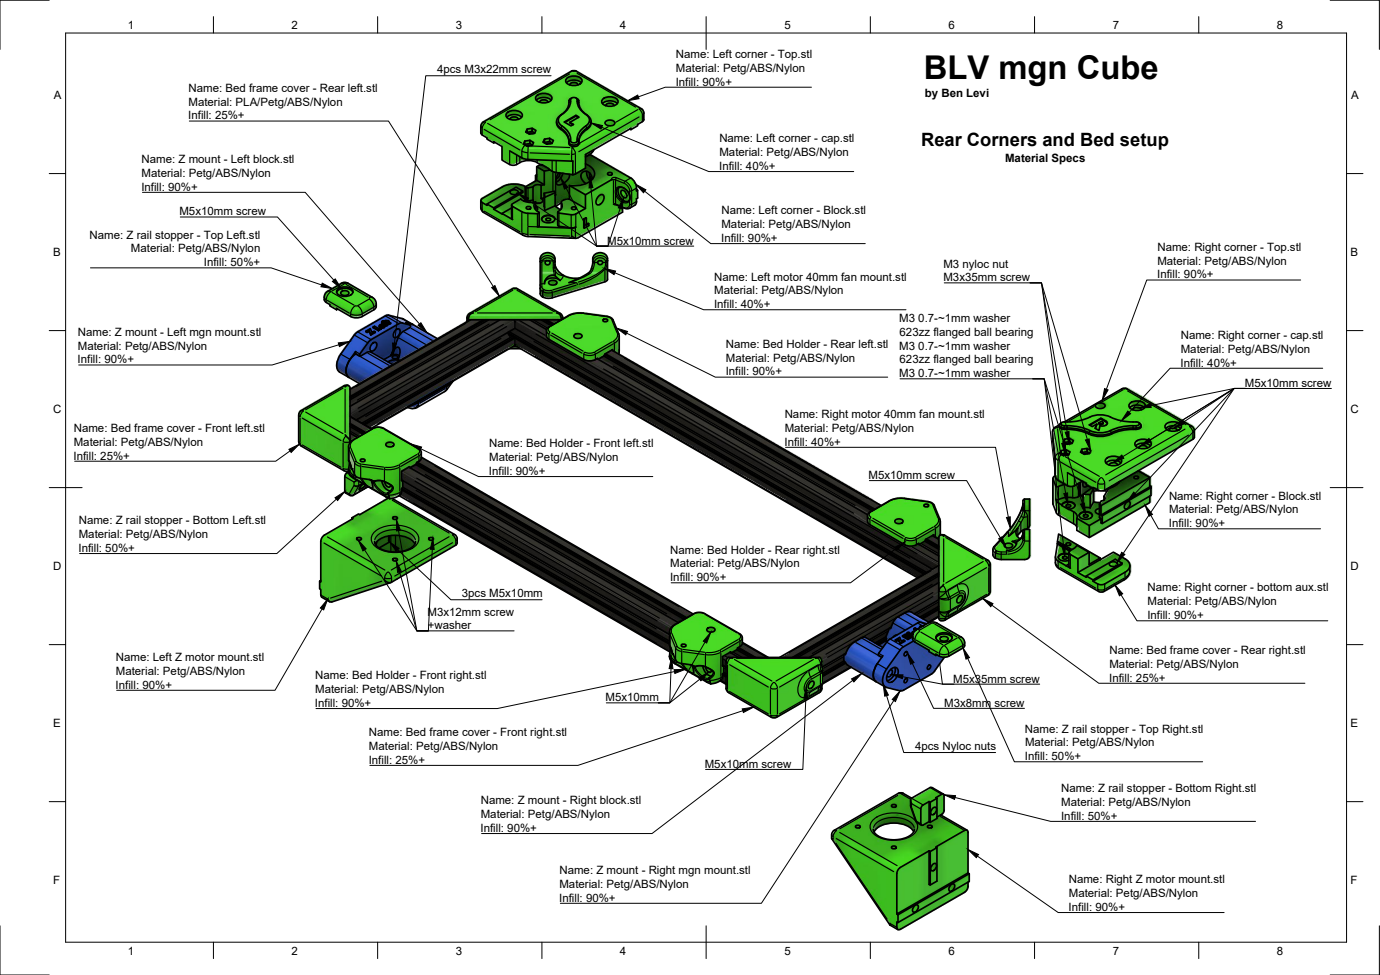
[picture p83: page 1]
Infill: 50%+; Material Specs; M5x10mm screw; 3pcs M5x10mm; 4pcs Nyloc nuts; 4pcs M3x22mm screw; M3x8mm screw; M5x35mm screw; M3x12mm screw; M3 nyloc nut M3x35mm screw

Name: Left corner - Top.stl
Material: Petg/ABS/Nylon
Infill: 90%+

BLV mgn Cube

Name: Bed frame cover - Rear left.stl
Material: PLA/Petg/ABS/Nylon
Infill: 25%+

by Ben Levi

Name: Left corner - cap.stl
Infill: 40%+

Rear Corners and Bed setup

Name: Z mount - Left block.stl

Name: Left corner - Block.stl

Name: Z rail stopper - Top Left.stl

Name: Right corner - Top.stl

Name: Left motor 40mm fan mount.stl

M3 0.7-~1mm washer
623zz flanged ball bearing

Name: Z mount - Left mgn mount.stl

Name: Right corner - cap.stl

Name: Bed Holder - Rear left.stl

Name: Bed frame cover - Front left.stl

Name: Right motor 40mm fan mount.stl

Name: Bed Holder - Front left.stl

Name: Right corner - Block.stl

Name: Z rail stopper - Bottom Left.stl
Infill: 50%+

Name: Bed Holder - Rear right.stl

Name: Right corner - bottom aux.stl

Name: Left Z motor mount.stl

Name: Bed frame cover - Rear right.stl

Name: Bed Holder - Front right.stl

Name: Z rail stopper - Top Right.stl

Name: Bed frame cover - Front right.stl

Name: Z rail stopper - Bottom Right.stl

Name: Z mount - Right block.stl

Name: Z mount - Right mgn mount.stl

Name: Right Z motor mount.stl

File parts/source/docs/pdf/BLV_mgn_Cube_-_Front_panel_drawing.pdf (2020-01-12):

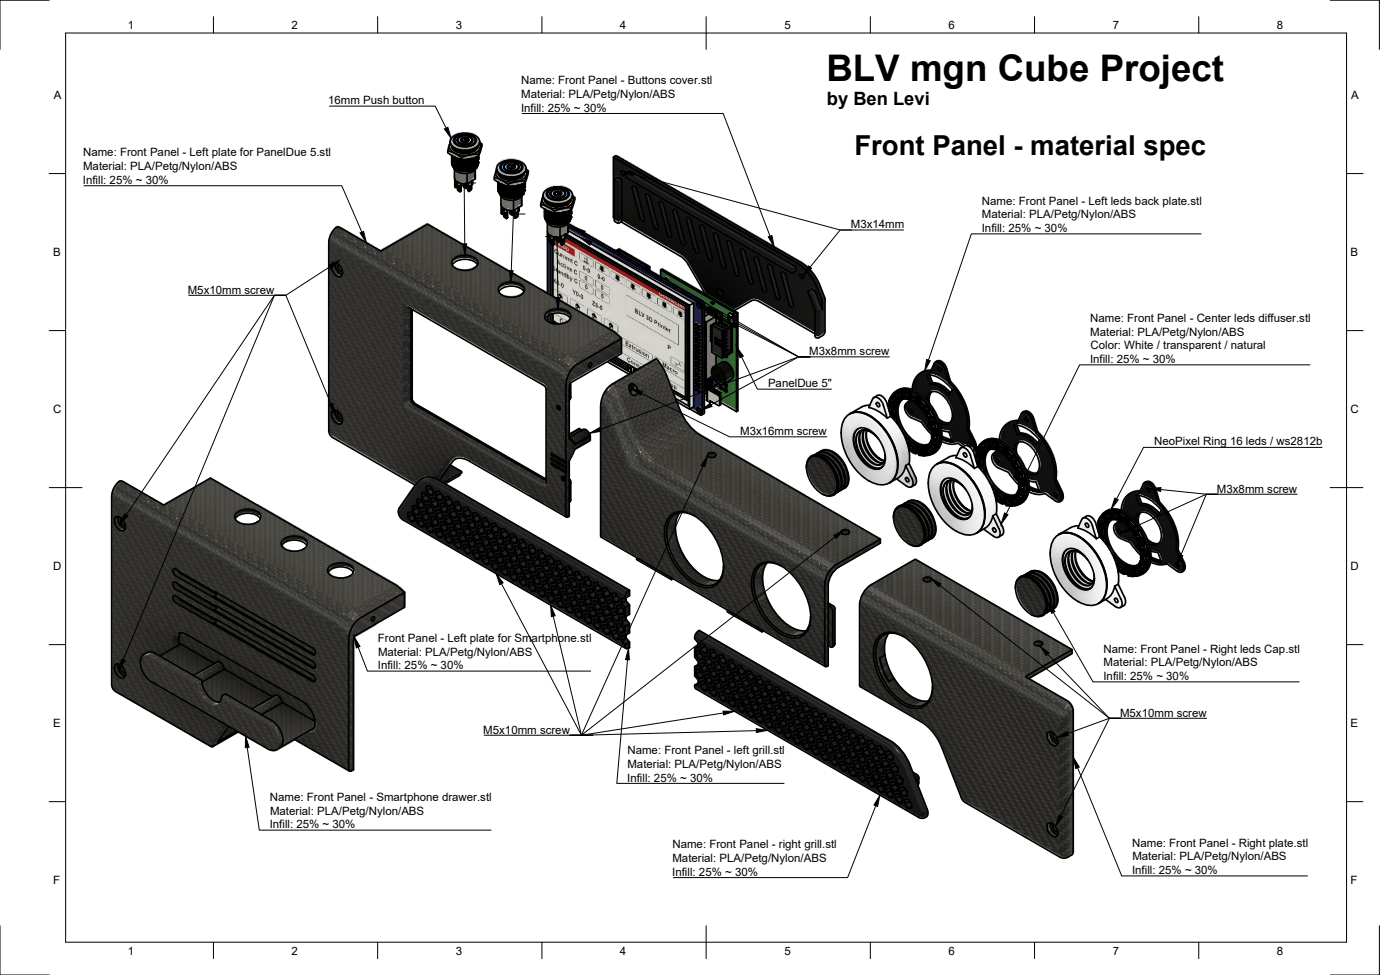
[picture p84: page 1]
PanelDue 5"; 16mm Push button; M5x10mm screw; M3x16mm screw; M3x8mm screw

BLV mgn Cube Project

Name: Front Panel - Buttons cover.stl
Material: PLA/Petg/Nylon/ABS
Infill: 25% ~ 30%

by Ben Levi
Front Panel - material spec

Name: Front Panel - Left plate for PanelDue 5.stl

Name: Front Panel - Left leds back plate.stl

Name: Front Panel - Center leds diffuser.stl
Color: White / transparent / natural

NeoPixel Ring 16 leds / ws2812b

Front Panel - Left plate for Smartphone.stl

Name: Front Panel - Right leds Cap.stl

Name: Front Panel - left grill.stl

Name: Front Panel - Smartphone drawer.stl

Name: Front Panel - Right plate.stl

Name: Front Panel - right grill.stl

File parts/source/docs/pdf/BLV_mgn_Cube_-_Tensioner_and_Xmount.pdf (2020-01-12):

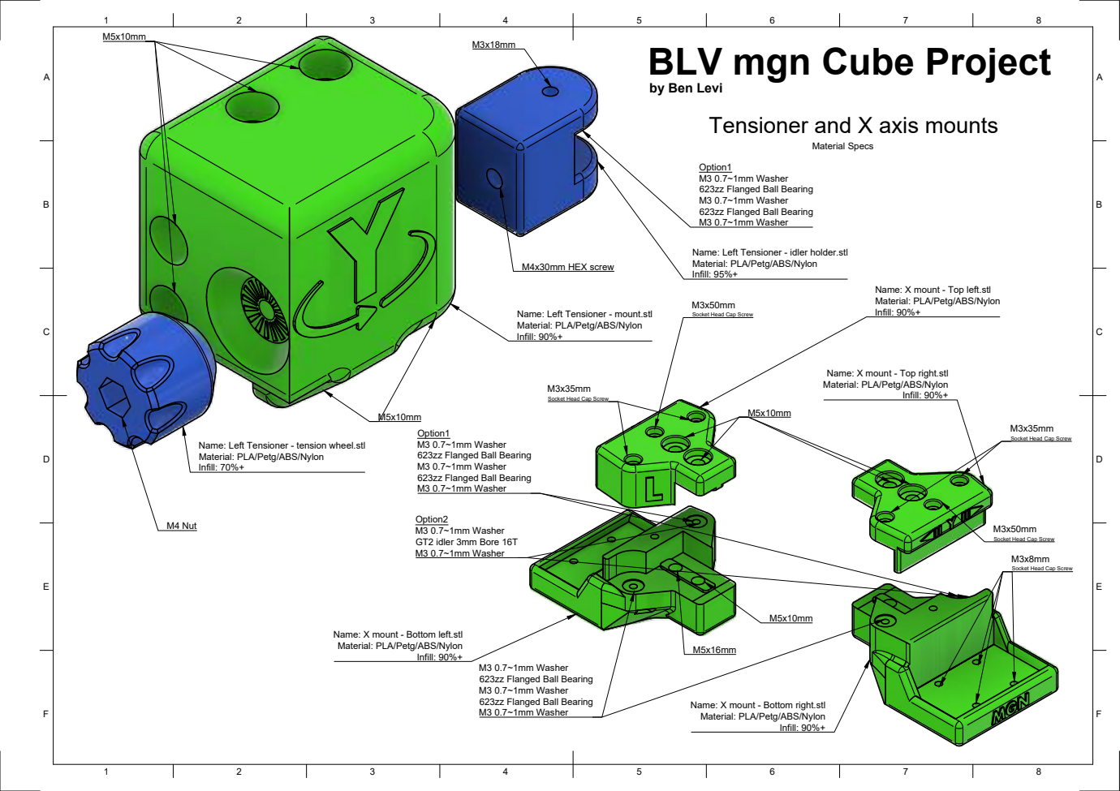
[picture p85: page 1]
Infill: 90%+; Material Specs; M3 0.7~1mm Washer GT2 idler 3mm Bore 16T M3 0.7~1mm Washer; M4 Nut; M4x30mm HEX screw

BLV mgn Cube Project

by Ben Levi
Tensioner and X axis mounts

Option1
M3 0.7~1mm Washer
623zz Flanged Ball Bearing

Name: Left Tensioner - idler holder.stl
Material: PLA/Petg/ABS/Nylon
Infill: 95%+

Name: X mount - Top left.stl
Infill: 90%+

Name: Left Tensioner - mount.stl

Socket Head Cap Screw

Name: X mount - Top right.stl

Name: Left Tensioner - tension wheel.stl
Infill: 70%+

Name: X mount - Bottom left.stl

Name: X mount - Bottom right.stl

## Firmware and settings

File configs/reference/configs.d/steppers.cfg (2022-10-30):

[stepper_x]
step_pin: P2.2
dir_pin: !P2.6
enable_pin: !P2.1
microsteps: 16
#rotation_distance: 16
rotation_distance: 32
endstop_pin: P1.29
position_endstop: -22
position_min: -22
position_max: 310
homing_speed: 70
homing_retract_dist: 5
full_steps_per_rotation: 400    # The number of full steps for one rotation of the stepper motor. 200 for 1.8 motor or 400 for 0.9 motor.

[tmc2208 stepper_x]
uart_pin: P1.10
run_current: 1.1
hold_current: 0.500
stealthchop_threshold: 0 # 0 = disabled
interpolate: True

[stepper_y]
step_pin: P0.19
dir_pin: !P0.20
enable_pin: !P2.8
microsteps: 16
rotation_distance: 32
#rotation_distance: 16
endstop_pin: P1.28
position_endstop: 310
position_max: 310
homing_speed: 70
homing_retract_dist: 5
full_steps_per_rotation: 400    # The number of full steps for one rotation of the stepper motor. 200 for 1.8 motor or 400 for 0.9 motor.

[tmc2208 stepper_y]
uart_pin: P1.9
run_current: 1.1
hold_current: 0.500
stealthchop_threshold: 0 # 0 = disabled
interpolate: True

[stepper_z]
step_pin: P0.22
dir_pin: !P2.11
enable_pin: !P0.21
microsteps: 16
rotation_distance: 8
endstop_pin: probe:z_virtual_endstop
#endstop_pin: !P1.27
#position_endstop: 0.0
position_min: -10 # For Z_TILT_ADJUST this is max tilt it will handle
position_max: 345
homing_speed: 10.0
homing_retract_dist: 3.0
homing_retract_speed: 20
second_homing_speed: 2.0
full_steps_per_rotation: 200    # The number of full steps for one rotation of the stepper motor. 200 for 1.8 motor or 400 for 0.9 motor.

[tmc2208 stepper_z]
uart_pin: P1.8
;run_current: 1
run_current: 0.650 ; Consider reducing this to 0.5
hold_current: 0.450
stealthchop_threshold: 0 # 0 = disabled
interpolate: True

[stepper_z1]
step_pin: P1.15
dir_pin: !P1.14
enable_pin: !P1.16
microsteps: 16
rotation_distance: 8
full_steps_per_rotation: 200    # The number of full steps for one rotation of the stepper motor. 200 for 1.8 motor or 400 for 0.9 motor.

[tmc2208 stepper_z1]
uart_pin: P1.1
;run_current: 1
run_current: 0.650
hold_current: 0.450
stealthchop_threshold: 0 # 0 = disabled
interpolate: True

[extruder]
step_pin: P2.13
dir_pin: !P0.11
enable_pin: !P2.12
microsteps: 16
gear_ratio: 50:17
rotation_distance: 22.62
full_steps_per_rotation: 200 # 200 for 1.8 Deg motor, 400 for 0.9 Deg motor
nozzle_diameter: 0.400
filament_diameter: 1.750
heater_pin: P2.7
sensor_type: ATC Semitec 104GT-2
sensor_pin: P0.24
#control: pid # Saved config using PID TUNE
#pid_Kp: 22.2
#pid_Ki: 1.08
#pid_Kd: 114
min_temp: 0
max_temp: 260
max_extrude_only_distance: 900.0
max_extrude_only_velocity: 60
pressure_advance = 0.48 ; 2nd try
;pressure_advance = 0.559 ; 1st try

[tmc2208 extruder]
uart_pin: P1.4
run_current: 1
hold_current: 0.500
interpolate: True
stealthchop_threshold: 0 # 0 = disabled
interpolate: True

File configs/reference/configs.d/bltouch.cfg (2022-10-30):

## BLTouch
[bltouch]
sensor_pin: ^P0.10  # Probe Pin, Pull-up (^ symbol) needed in open drain mode
control_pin: P2.0 # This is the Servo Pin
x_offset: 27.3
y_offset: -5.1
#z_offset: 1.4 # This is saved automatically in eeprom
pin_move_time: 1
stow_on_each_sample: false
probe_with_touch_mode: true
speed: 10 # Probing speed
samples: 2 # How many times to probe the same point
sample_retract_dist: 2.0 # How far to retract (in mm) from the probe point
samples_result: median
samples_tolerance: .02
samples_tolerance_retries: 5

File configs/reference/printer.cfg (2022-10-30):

# Customized klipper config for jsaintrocc's myblvmgncube
# originally based on Ben Levi's klipper.cfg http://www.blvproject.com

# This configuration is specific to this BoM
# * BTT SKR 1.4 Turbo
# * BTT Trinamic 2208 Drivers
# * BTT TFT35v3 Screen
# * 0.9 degree Steppers for X/Y
# * 1.8 degree Steppers for Z/E0
# * Bltouch V3.1
# * Dual independent Z steppers (Z/E1)

[printer]
kinematics: corexy
max_velocity: 300 ; BLV is 350
max_accel: 7000 ; BLV is 9000, Voron1 is 3000
max_z_velocity: 15 ; BLV is 20, Voron1 is 15
max_z_accel: 50 ; BLV is 150, Voron1 is 50
;max_accel_to_decel: 9000 ; BLV Setting
;square_corner_velocity: 5 ; The default
## Pulled these configs from voron1 but upped accel from 3K to 7K

[mcu]
baud: 250000
serial: /dev/serial/by-id/usb-Klipper_lpc1769_02D0000EC09869AFADCA405EC02000F5-if00

[fan]
pin: P2.3

[idle_timeout]
timeout: 1800

[input_shaper]
;shaper_freq_x: 36.84
;shaper_freq_y: 36.84
;shaper_freq_x: 42
;shaper_freq_y: 42
shaper_freq_x: 42.77
shaper_freq_y: 42.77

[virtual_sdcard]
path: ~/.octoprint/uploads/

[include configs.d/*.cfg] ; Include all config files in this directory
# z_offset = 1.599

#*# <---------------------- SAVE_CONFIG ---------------------->
#*# DO NOT EDIT THIS BLOCK OR BELOW. The contents are auto-generated.
#*#
#*# [bltouch]
#*# z_offset = 1.550
#*#
#*# [bed_mesh default]
#*# version = 1
#*# points =
#*# 	  0.316250, 0.170000, 0.190000, 0.320000
#*# 	  0.177500, 0.052500, 0.058750, 0.177500
#*# 	  0.168750, 0.001250, 0.043750, 0.167500
#*# 	  0.260000, 0.085000, 0.160000, 0.315000
#*# tension = 0.2
#*# min_x = 10.0
#*# algo = lagrange
#*# y_count = 4
#*# mesh_y_pps = 2
#*# min_y = 5.0
#*# x_count = 4
#*# max_y = 299.99
#*# mesh_x_pps = 2
#*# max_x = 299.98
#*#
#*# [extruder]
#*# control = pid
#*# pid_kp = 23.827
#*# pid_ki = 1.346
#*# pid_kd = 105.436
#*#
#*# [heater_bed]
#*# control = pid
#*# pid_kp = 73.104
#*# pid_ki = 0.771
#*# pid_kd = 1732.566

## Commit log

2020-01-13 X-Carriage Notes and configs
    [X-Carriage-Group-1.3mf, X-Carriage-Group-2-PLA.3mf]
2020-02-01 Initial commit of source with some organization done
    [2020_Jig.stl, 2040_Jig.stl, 4010_Spitfire_cover.stl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]
2020-02-01 Added step for extruder mount
    [Extruder__-_bondtech_Rear_mount_REMIX.step]
2020-02-01 Fixed extension
    [X_carriage_-_Block_shield_REMIX.step]
2020-02-02 Remaining steps for cad file hotend
    [X_carriage_-_Block_shield_REMIX.step, X_carriage_-_Bottom_REMIX.step, X_carriage_-_Cable_locker_REMIX.step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]
2020-02-02 Fixed CAD file
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2020-12-07 imported source docs and new prusaslicer profiles
    [BLV_mgn_Cube-Frame_calculator.xlsx, BLV_mgn_Cube_-_Enclosure_Vector_file.dxf, BLV_mgn_Cube_-_Panels_-_Walls_dimensions.dwg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]
2020-12-14 Added 3mf files and notes for rest of rear corners and also Tensioner
    [All_Z_motor_mount.3mf, BLV_mgn_Cube-Frame_calculator.xlsx, Bed_Holder_-_All_For_CR-10_bed_M4_screw.3mf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]
2020-12-17 Organized 3mf files and started spreadsheet for printing parts
    [2020_2040_Jigs.3mf, Air_scrubber_-_main_box.3mf, All_Z_motor_mount.3mf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]
2020-12-24 Added remixed Panel parts
    [BLV MGN Cube 365MM Z BOM.xlsx, Center_Plate.3mf, Center_plate_Rework.3mf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]
2021-01-08 Added peanel 3mfs and Bear inspired README
    [Left_Grill_Rework.3mf, My_BoM.xlsx, Right_Grill_Rework.3mf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]
2021-01-17 Updated with comments from Anatoly and David
    [My_BoM.xlsx]
2021-01-22 Step 2 and Feet STL
    [Front_Panel_-_Center_plate.STL, Front_Panel_-_Left_plate_for_TFT35_V2.STL, Front_Panel_-_Right_plate.STL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]
2021-01-23 More updates to step 3 and started work on Bom
    [My_BoM.xlsx]
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2021-01-25 Added L and R Mirrored parts
    [FootLv2.stl, FootRv2.stl]
2021-01-25 Cut down by 2mm to prevent from hitting extrusions
    [FootLv2.stl, FootRv2.stl]
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2021-02-11 Added step 5 build y axis. Updated BoM.
    [2020_2040_Jigs.3mf, Bottom_X_Plate.3mf, Front_and_Back_Plate.3mf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]
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2021-02-21 Added extruder carrage part a
    [Top_and_Bottom_Plate.3mf]
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2021-03-08 Fixed carriage typeO
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2021-04-11 Added Z axis frame steps and BoM
    [Jig_Main.3mf]
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2021-05-05 Added missing motor mount picture
2021-05-23 Add missing M3s for back corner stepper attachment
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2021-05-29 Modified Hotend cable locker
    [Foot v6.f3d, Hotend Cable Locker v4.stl]
2021-05-31 Create X-carriage-cable-locker v5.stl
    Revised X carriage cable locker
    [X-carriage-cable-locker v5.stl]
2021-05-31 Create X-carriage-cable-locker v7.stl
    New version with slightly wider base and smaller middle hole
    [X-carriage-cable-locker v7.stl]
2021-05-31 Create Frame-cable-locker v2.stl
    1st draft of frame calbe locker
    [Frame-cable-locker v2.stl]
2021-06-01 Create Frame-cable-locker v4.stl
    Added lower cable strap
    [Frame-cable-locker v4.stl]
2021-06-01 Create Frame-cable-locker v5.stl
    Fixed missing extrude
    [Frame-cable-locker v5.stl]
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2021-06-04 Added cable locker parts and source
    [Extruder__-_bondtech_Rear_mount_REMIX.step, Frame-cable-locker v2.stl, Frame-cable-locker v4.stl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]
2021-06-14 Create dinrailmount-v2.stl
    Experimental part
    [dinrailmount-v2.stl]
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2021-07-14 cleanup and new skr14 din rail mount
    [HB-Relay-dinrailmount v5.stl, HB-Relay-dinrailmount.stl, dinrailmount-v2.stl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]
2021-07-17 renamed skr din rail mount with dimension
    [skr14v2-dinrailmount35_5mm.stl]
2021-07-17 different size din clamps
    [skr14v2-dinrailmount-37_5mm.stl, skr14v2-dinrailmount-37mm.stl]
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2021-08-01 Create conduit-reinforcer v1.stl
    [conduit-reinforcer v1.stl]
2021-08-05 Create conduit-reinforcer v2.stl
    [conduit-reinforcer v2.stl]
2021-08-05 Update conduit-reinforcer v2.stl
    [conduit-reinforcer v2.stl]
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2021-08-08 Tweaks for wire management parts
    [Frame-cable-locker v9.stl, conduit-reinforcer-long v2.stl, wire-manager-ziptie2 v7.stl]
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2021-08-08 Create conduit-reinforcer-long v3.stl
    [conduit-reinforcer-long v3.stl]
2021-08-09 updated for 24" zip ties
    [Frame-cable-locker v12.stl, X-carriage-cable-locker v11.stl, wire-manager-ziptie2 v9.stl]
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2021-08-12 Create extruder mount v5.stl
    [extruder mount v5.stl]
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2021-08-14 Added hotend cable locker parts
    [conduit-reinforcer.stl, extruder-mount.stl, frame-hotend-cable-locker.stl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]
2021-08-14 fixed guide to use hotend instead of extruder in the instructions
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2021-08-20 Hotend wiring and cable management system. FINALLY DONE!!
    [flex-tube-reinforcer.stl]
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2021-09-05 added skr mount stl
    [skr14-dinrailmount.stl]
2021-09-09 Oops wrong branch
    [Y-Endstop-for-kw11-3p.stl]
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2021-09-13 updated bed plate bom and added leveling knob parts
    [BLV_Thumbwheel_bed_leveling_knob.3mf, BLV_Thumbwheel_bed_leveling_knob.stl]
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2021-09-15 added 3mf files for endstop
    [Y-Endstop-for-kw11-3p-ABS.3mf, Y-Endstop-for-kw11-3p-PETG.3mf]
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2022-02-21 Added Slotted Wiring Duct STLs and added prep procedure.
    [Slotted_Wire_Duct100mm_Slotted_Wire_Duct_v17_Bottom_1_Body1_Bottom.stl, Slotted_Wire_Duct100mm_Slotted_Wire_Duct_v17_Left_Side_1_Body20_Left_Side.stl, Slotted_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]
2022-02-21 Fixed bad STL links
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2022-05-24 Added din mounts and some updates for wiring the panel
    [MOSFET_Long2.stl, MOSFET_Mount.stl, rPi_DIN_Mount_v4.stl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]
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2022-09-03 Minor fixes and organizing stls
    [Main_Cable_Tube_Holder_JSR.f3d, Main_Cable_Tube_Holder_JSR.stl, X_carriage_-_Cable_locker_JSR.f3d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]
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2022-09-03 Fix line breaks for new BoM Links
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2022-09-13 9 combine and revise the print settings.md (#45)
    * Reference google sheet for print settings
    * Reference google sheet for print settings
    * updated 3mf name to new convention
    * Remove obsolete 3mf files
    [Air_scrubber_-_main_box.3mf, BLV MGN Cube 365MM Z BOM.xlsx, BMG_Rear_Mount.3mf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]
2022-09-24 30 add instruction on squaring your x axis against the front tensioners (#47)
    * inital printer tuning doc
    * Added alpha belt tuning procedure
    * Final belt tuning procedure
    * Added lock removal images and 3d part 3mfs
    [GT2-6mm-Belt-Tension-Tool-PLA.3mf, GT2-6mm-Belt-Tension-Tool.stl, X-Carriage-Clamp-PLA.3mf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]
2022-09-24 Fixed missing 3mfs
    [X_mount_-_Top_left-ABS.3mf, X_mount_-_Top_right-ABS.3mf]
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2022-10-30 Fixed video link
    [bed.cfg, bedadjust.cfg, bltouch.cfg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]
